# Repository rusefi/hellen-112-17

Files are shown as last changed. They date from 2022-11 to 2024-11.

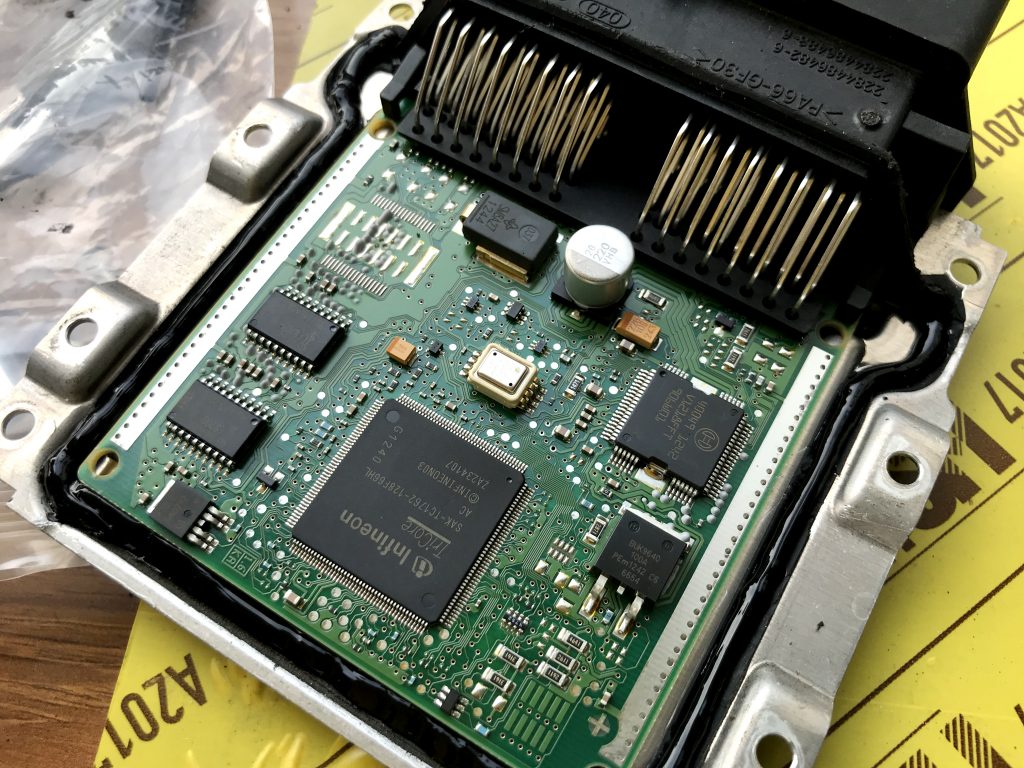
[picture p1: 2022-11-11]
docs/oem.jpg

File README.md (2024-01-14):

# hellen-112-17

[User Documentation](https://github.com/rusefi/rusefi/wiki/Hellen112-17)

[Interactive Pinout](https://rusefi.com/docs/pinouts/hellen/hellen-112-17/)

[Firmware Source Code](https://github.com/rusefi/rusefi/tree/master/firmware/config/boards/hellen/hellen-112-17)

# Compatibility

Bosch 21126-1411020-45

Bosch 21126-1411020-49

Bosch 21126-1411020-70

Suzuki 33910-69L01

Polaris Slingshot 4015316

Maybe 391F2-03FA0 HYUNDAI I20 1.2 16V?

Maybe 39124-2B500 KIA FORTE 1.6?

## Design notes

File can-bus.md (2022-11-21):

https://trekberry.ru/stat/rabota_s_can_shinoi_na_avtomobilie_lada_granta

ID 481 1 байт Двери 0 Закрыта, 128 Дверь водителя, 32 пасажира,160 передние двери открыты

ID 481 3 байтаварийка открытие багажника 31 поворотник на право2 поворотник на лево

ID 421 1 байт8 паркинг16 задняя24 нейтралка32 драйв72 2 скорость64 1 скорость

ID 498 1 байт ремень волителя65 пристегнут64 нет

ID 2DE 3 байт ручник0 опущен1 поднят5 или 4 включен ближний свет

ID 481 4 байт 1 моргнуть дальним

ID 160 6 байт педаль газа

ID 255 отпущена56 нажна в пол

==================
https://habr.com/ru/post/653615/

BU_: ECM ABS SRS 
BO_ 384 ECM_180: 8 ECM
   SG_ rpm : 7|16@0+ (0.125,0) [0|0] "rpm" Vector__XXX

BO_ 505 ECM_1F9: 8 ECM
   SG_ speed_km_h : 23|16@0+ (0.01,0) [0|0] "" Vector__XXX

BO_ 852 ABS_354: 8 ABS
   SG_ abs_lamp_on : 55|1@0+ (1,0) [0|1] "" Vector__XXX

BO_ 1176 SRS_498: 1 SRS
   SG_ airbag_lamp : 4|1@1+ (1,0) [0|0] "" Vector__XXX
   SG_ seatbelt_fastened : 0|1@1+ (1,0) [0|0] "" Vector__XXX

BO_ 1361 ECM_551: 8 ECM
   SG_ coolant_temperature : 15|8@0+ (1,-40) [0|0] "" Vector__XXX
   SG_ check_engine_lamp_on : 32|1@1+ (1,0) [0|0] "" Vector__XXX
   SG_ check_engine_lamp_blinking : 33|1@1+ (1,0) [0|0] "" Vector__XXX
   SG_ oil_lamp_on : 34|1@1+ (1,0) [0|0] "" Vector__XXX
   SG_ overheat_lamp_with_sound : 35|1@1+ (1,0) [0|0] "" Vector__XXX
   SG_ battery_lamp_off : 24|1@1+ (1,0) [0|0] "" Vector__XXX

   ==============================

   0x160 — педаль газа, дроссель
0x180 — обороты мотора, некоторые параметры по мотору
0x280 — приборы, скорость
0x481 — двери, световые приборы, подогревы
0x551 — приборы
0x555 — климат-контроль
0x560 — АКП

=======================

https://habr.com/ru/post/479672/comments/#comment_24929006



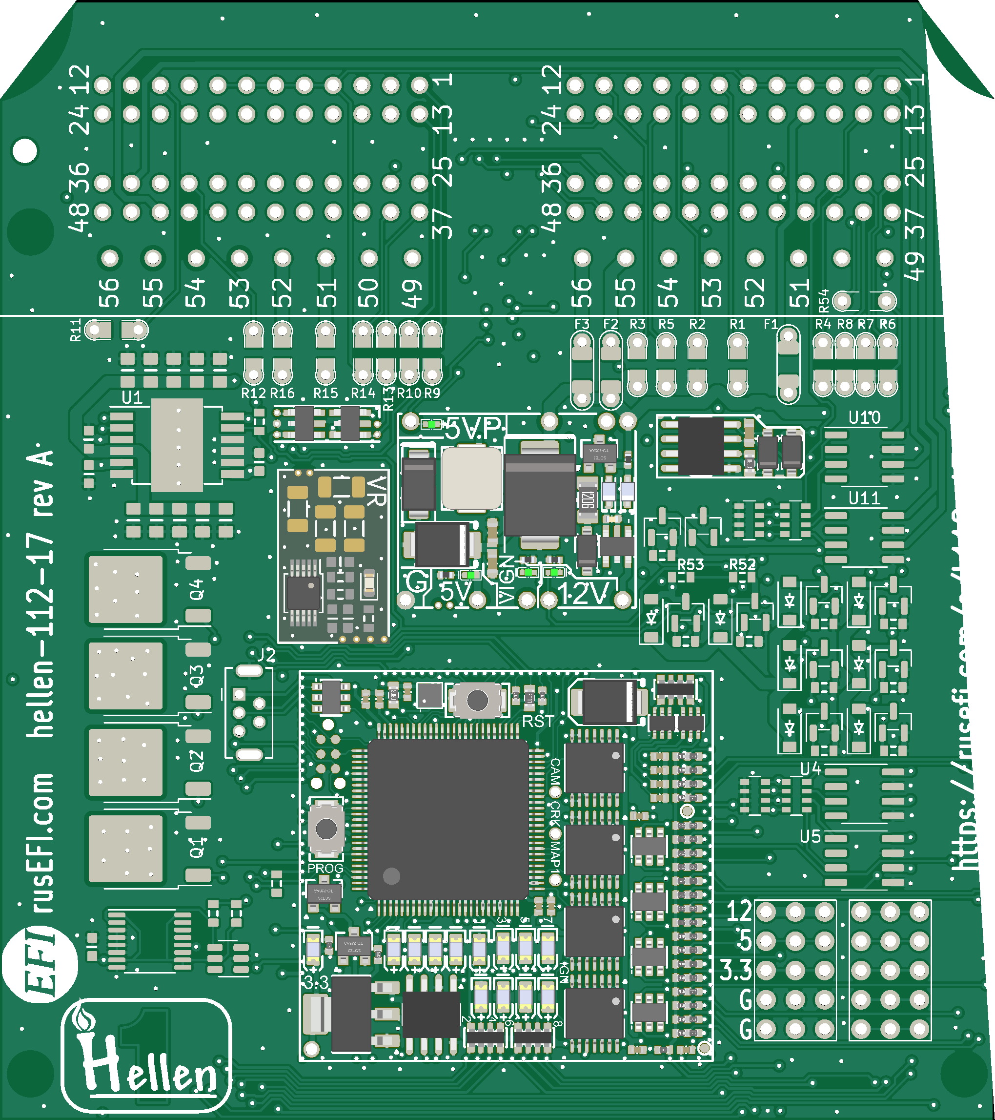
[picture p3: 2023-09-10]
boards/hellen-112-17-a/board/hellen-112-17-a.png

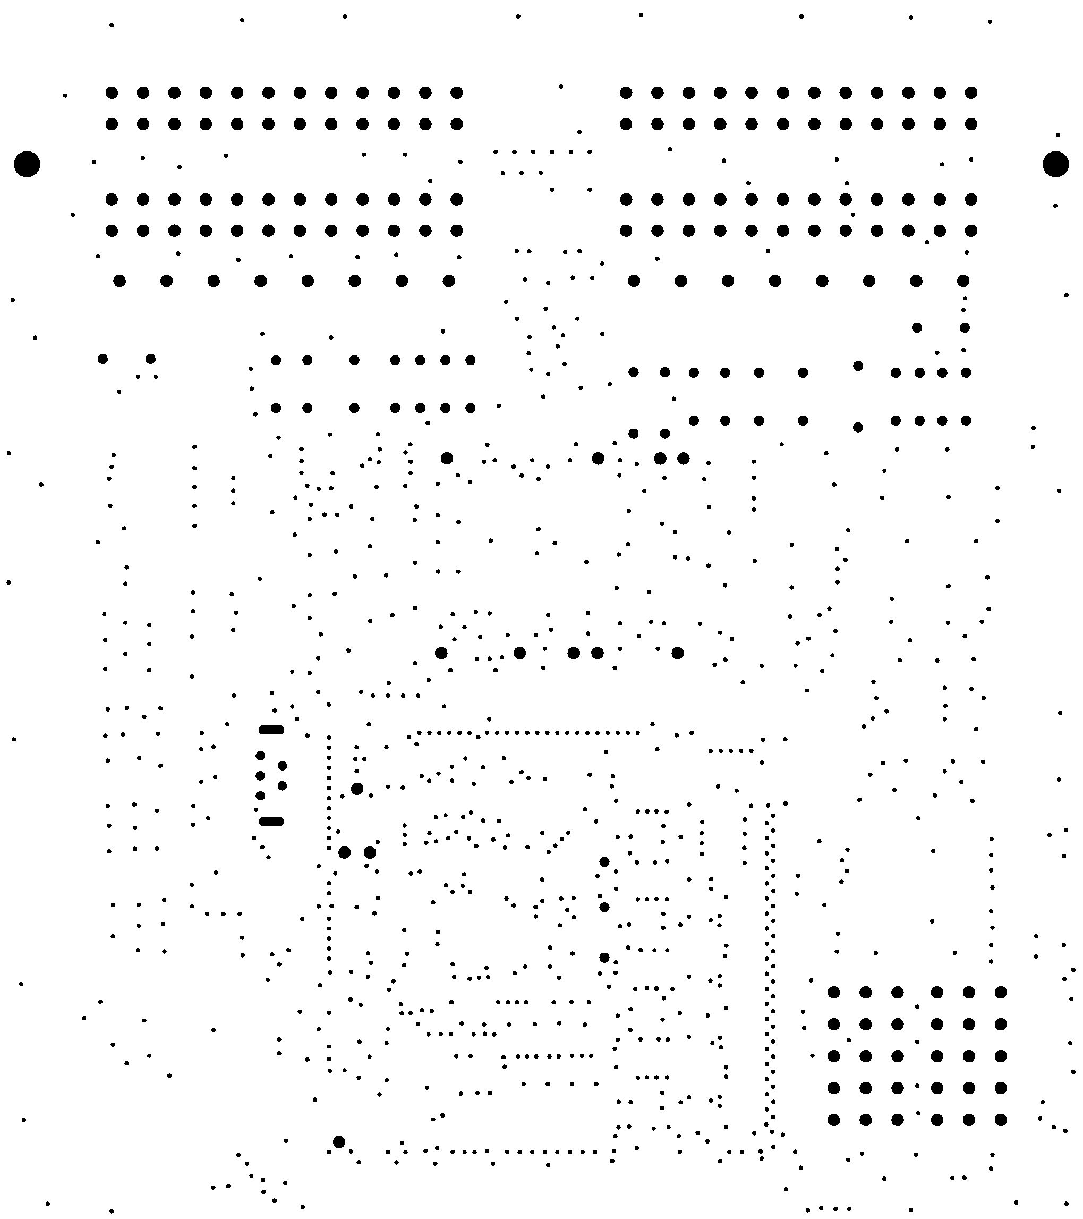
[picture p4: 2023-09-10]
boards/hellen-112-17-a/board/misc/hellen-112-17-a-outline.png

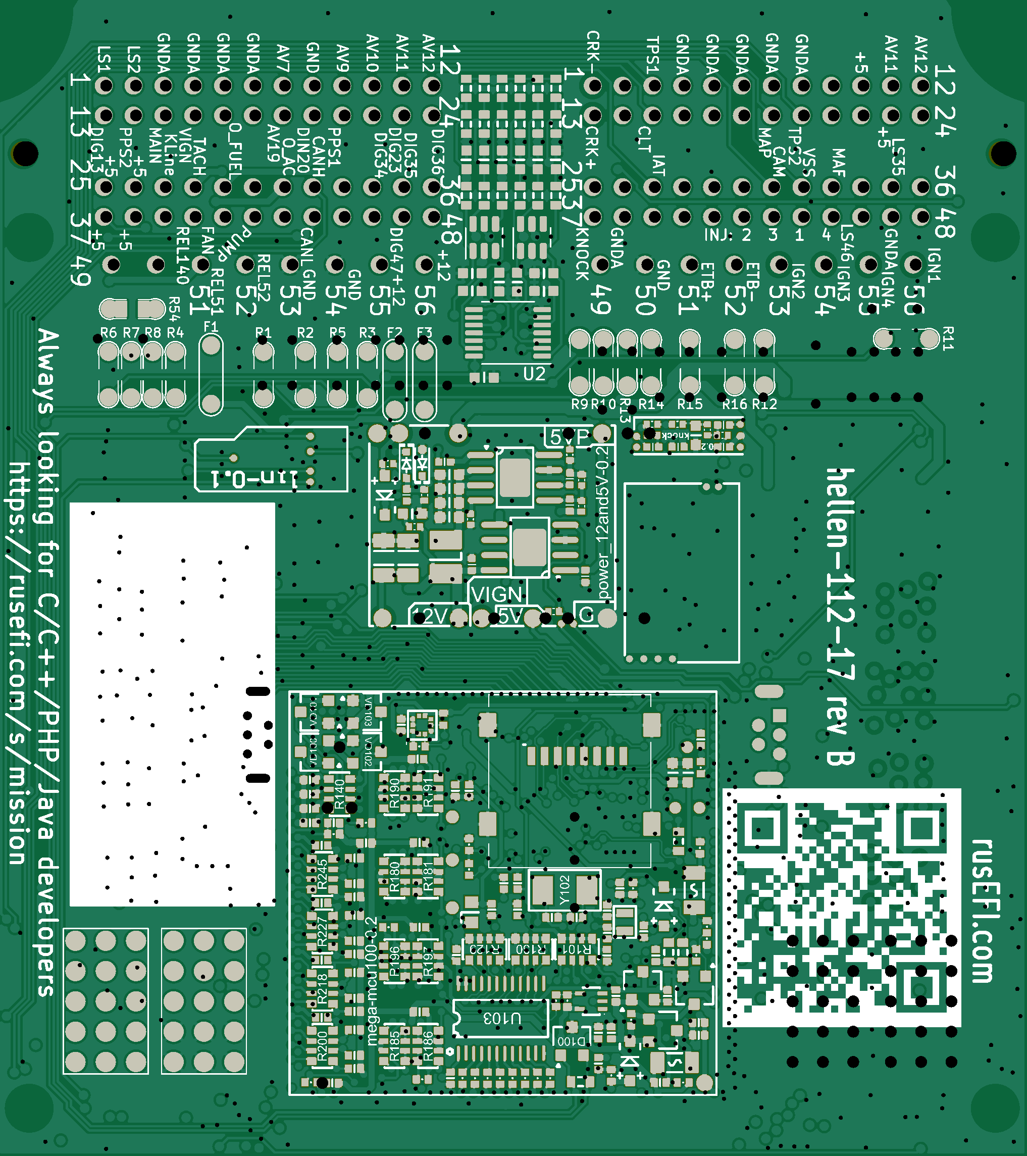
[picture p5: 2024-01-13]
boards/hellen-112-17-b/board/misc/hellen-112-17-b-bottom.png

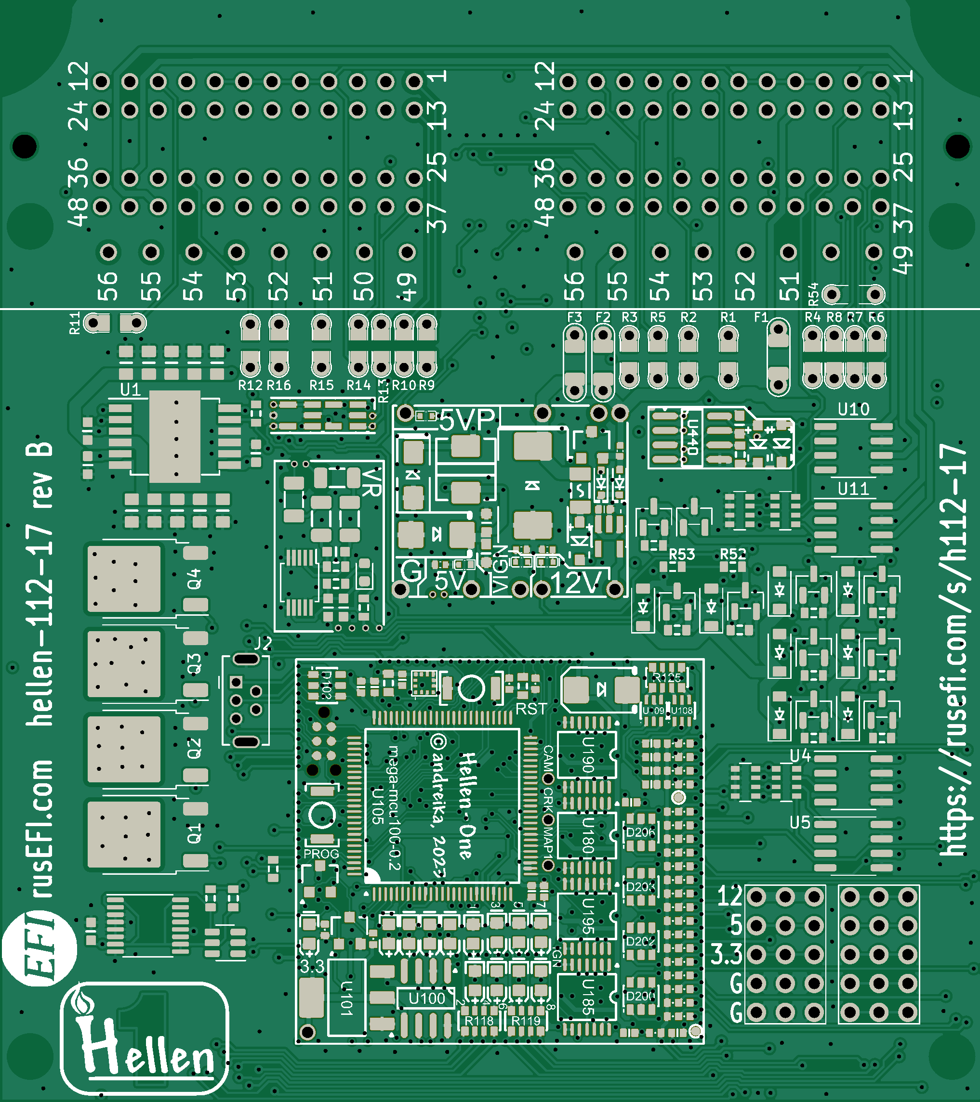
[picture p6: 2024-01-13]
boards/hellen-112-17-b/board/misc/hellen-112-17-b-top.png

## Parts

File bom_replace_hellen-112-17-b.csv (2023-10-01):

# remove +5V pull-ups from SPI1, because we use it with +3.3v accelerometer
R103,
R105,
# remove jumper resistor connecting BOOT1 with A22 input line, because we use STM32F4
R131,
#CAN wakeup disabled, O2S input enabled
R145,
#PWR_EN not used as GPIO
R142,
#IGBT series resistor
"R114, R115, R116, R117","33","R0402","C25105"
# DC-DC Inductor
L421,"MWSA0503S-100MT","MWSA0503","C408412"
# fuses
F410,"nSMD050-24V","SMD1206","C70076"
# TLS115
U411,"TLS115B0EJXUMA1","PG-DSO-8","C3743696"
# no software for accelerometer
U106,
# STM32F407VGT6 is very cheap
U105,"STM32F429VGT6","LQFP100","C12345"
#include hellen-one/board_id/generated/board_id_h112-17-b.csv
#include bom_pullups_hellen-112-17-b.csv

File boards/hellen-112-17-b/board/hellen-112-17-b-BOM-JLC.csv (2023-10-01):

Comment | Designator | Footprint | LCSC Part #
10u | C1, C2, C3, C4, C5, C6, C7, C8, C9, C10 | C0805 | C15850
100n | C11, C14, C21, C772, C440 | C0603 | C14663
10n | C12, C13 | C0603 | C57112
1n | C15, C16, C17, C18, C19, C20, C22, C23, C24, C25, C26, C28, C771 | C0603 | C1588
PSM712-LF | D1, D411 | SOT-23 | C32677
B5819W | D2, D3, D4, D5, D6, D7, D8, D9, D416, D417, D101, D107, D440, D441 | SOD-123 | C8598
SRV05-4-P-T7 | D10, D11, D12, D102, D200, D202, D203, D206 | SOT23-6 | C85364
12H1500D | F1, F2, F3 | PAD-1206-PAD | C182446
USB_B_Mini | J2 | USB-MINI-B-VERTICAL | C13453
ISL9V3040D3S | Q1, Q2, Q3, Q4 | DPAK | C462128
AO3400A | Q5, Q6, Q7, Q8, Q9, Q10, Q11, Q12, Q13, Q101, Q103 | SOT-23 | C20917
Jumper-Pad-Pad | R1, R2, R3, R4, R5, R6, R7, R8, R9, R10, R11, R12, R13, R14, R15, R16, R54 | PAD-0805-PAD | C17477
4.7k | R17, R18, R19, R20, R25, R26, R27, R28, R33, R34, R35, R36, R37, R38, R39, R40, R41, R50, R51, R52, R53 | R0603 | C23162
10k | R30, R31, R32, R42, R43, R48, R776, R777 | R0603 | C25804
1k | R44, R45, R46, R47 | R_Array_Convex_4x0603 | C20197
TLE9201SG | U1 | Infineon_PG-DSO-12-11 | C112633
74HC14PW,118 | U2 | TSSOP14 | C5606
VNLD5160 | U4, U5, U10, U11 | SO8 | C377942
74VHC163FT | U7 | TSSOP-16_4.4x5mm_P0.65mm | C150161
47u | C410, C412 | C1206 | C96123
100n | C411, C413, C420, C470 | C0402 | C307331
1u | C414, C415, C133 | C0402 | C52923
10u | C421, C422, C423, C424, C425, C426 | C0603 | C96446
4.7u | C427 | C0603 | C19666
10n | C428, C209, C203, C202, C201, C200, C214, C215, C212, C213, C225, C226, C227, C228, C145, C146 | C0402 | C15195
220p | C429 | C0402 | C1530
1N4148WS | D410, D412, D413, D414 | SOD-323 | C2128
SMCJ30A | D418 | SMC | C310046
SS34 | D420 | SMA | C8678
P6SMB6.8CA | D421, D205 | SMB | C78395
2.2uH | L420 | L1210 | C36828
MHT136UGCT | LED1, LED2, LED3, LED4 | LED0402 | C434447
6.8k | R410, R413 | R0402 | C25917
33k | R411, R424, R425, R474 | R0402 | C25779
1 | R420 | R0402 | C25086
10k | R421, R426, R427, R102, R107, R108, R109, R121, R127, R128, R141 | R0402 | C25744
68k | R422 | R0402 | C36871
12k | R423, R472 | R0402 | C25752
4.7k | R428, R144, R202, R201, R124, R126, R132, R135 | R0402 | C25900
MIC5205-3.3YM5 | U410 | SOT23-5 | C37970
LMR14020 | U420 | SOP8 | C187824
22u | C773, C117, C123 | C0603 | C59461
LED-GREEN-0603 | D771, D104, D108 | LED-0603 | C72043
4.7k | R771, R772, R773, R774 | R1206 | C17936
MAX9924UAUB+ | U771 | MSOP-10_3x3mm_P0.5mm | C143633
3.3n | C471 | C0402 | C26404
330p | C472 | C0402 | C13533
47p | C473 | C0402 | C1567
680p | C474 | C0603 | C1630
470k | R470 | R0402 | C25790
100k | R471, R473 | R0402 | C25741
LMV321IDBVR | U470, U471 | SOT23-5 | C7972
TJA1051T/3/1J | U100 | SO8 | C38695
SN74LVC4245APWR | U103 | TSSOP24 | C7859
SN74LVC1G06DCKR | U110 | SOT-353 | C7828
SMD1206B035TF/16 | F100, F101 | R1206 | C269114
REF3033 | U102 | SOT-23 | C36658
PESD1CAN | D100 | SOT-23 | C343993
Molex MicroSD 47219-2001 | J100 | SDAMB-012 | C164170
MCP6004 | U180, U185, U190, U195 | TSSOP14 | C50282
LPS22HBTR | U107 | HLGA-10L | C94049
LED-YELLOW-0603 | D106 | LED-0603 | C72038
LED-RED-0603 | D103 | LED-0603 | C2286
LED-BLUE-0603 | D105, D109, D110, D111, D112, D113, D114, D115, D116 | LED-0603 | C72041
LDL1117S33R | U101 | SOT-223 | C435835
BTN | S100, S101 | SMD-2_2.9x3.9x1.7 | C115357
BLM18AG601SN1D | L100 | L0603 | C19330
BAT54S | VD100, VD101, VD102, VD103 | SOT-23 | C47546
AO3401A | Q100, Q102 | SOT-23 | C15127
680k | R224, R208, R207, R234, R235, R232, R233, R250, R251, R252, R253, R225 | R0402 | C163456
510 | R254, R255, R256, R258 | R0402 | C25123
470 | R101, R118, R119 | R0603-4 | C25510
120 | R100 | R0603 | C22787
100n | C100, C101, C105, C108, C111, C112, C113, C119, C120, C122, C124, C126, C127, C130, C134, C147, C180, C185, C190, C195, C220, C221, C222 | C0402 | C1525
100 | R104, R106 | R0603 | C22775
74LVC2G17GW,125 | U108, U109 | SOT-363 | C80500
33k | R120 | R0603 | C4216
32.768 kHz | Y101 | SMD2012 | C99009
20 MHz | Y102 | SMD5032 | C112566
18p | C132, C136 | C0402 | C1549
12p | C115, C116 | C0402 | C1547
10k | R129, R130, R140 | R0603-4 | C29718
10 | R110, R111, R112, R113 | R0402 | C25077
5.1k | R195 | R0402 | C25905
4.7u | C102, C103, C104, C106, C107, C137, C138, C140 | C0402 | C23733
4.7k | R125, R180, R181, R185, R186, R190, R191, R196, R197, R200, R218, R227, R245 | R0603-4 | C66697
2.2u | C114, C131, C223, C224, C229 | C0402 | C12530
2.2k | R122, R123, R146, R147 | R0402 | C25879
1n | C135, C139, C141, C142, C211, C208, C210, C143, C144 | C0402 | C1523
0 | R143, R148 | R0402 | C17168
1k | R440 | R0603 | C21190
TJA1021T/20/CM | U440 | SO8 | C128810
33 | R114, R115, R116, R117 | R0402 | C25105
MWSA0503S-100MT | L421 | MWSA0503 | C408412
nSMD050-24V | F410 | SMD1206 | C70076
TLS115B0EJXUMA1 | U411 | PG-DSO-8 | C3743696
STM32F429VGT6 | U105 | LQFP100 | C12345
750 | R133 | R0603 | C23241
6800 | R134 | R0603 | C23212

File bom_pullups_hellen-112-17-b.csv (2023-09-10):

#CRANK CRANK_VR: UP DNP 1n
R222,
R226,
C211,"1n","C0402","C1523"
#CAM AV_107: DOWN 680k 10n
R220,
R224,"680k","R0402","C163456"
C209,"10n","C0402","C15195"
#VSS MAF: UP DNP 1n
R219,
R223,
C208,"1n","C0402","C1523"
#TPS TPS1: DOWN 680k 10n
R204,
R208,"680k","R0402","C163456"
C203,"10n","C0402","C15195"
#PPS PPS1: DOWN 680k 10n
R203,
R207,"680k","R0402","C163456"
C202,"10n","C0402","C15195"
#IAT IAT: UP 4.7k 10n
R202,"4.7k","R0402","C25900"
R206,
C201,"10n","C0402","C15195"
#CLT CLT: UP 4.7k 10n
R201,"4.7k","R0402","C25900"
R205,
C200,"10n","C0402","C15195"
#O2S TPS2: DOWN 680k 10n
R230,
R234,"680k","R0402","C163456"
C214,"10n","C0402","C15195"
#O2S2 PPS2: DOWN 680k 10n
R231,
R235,"680k","R0402","C163456"
C215,"10n","C0402","C15195"
#MAP1 MAP: DOWN 680k 10n
R228,
R232,"680k","R0402","C163456"
C212,"10n","C0402","C15195"
#MAP2 AV_109: DOWN 680k 10n
R229,
R233,"680k","R0402","C163456"
C213,"10n","C0402","C15195"
#AUX1 AV_110: DOWN 680k 10n
R246,
R250,"680k","R0402","C163456"
C225,"10n","C0402","C15195"
#AUX2 AV_111: DOWN 680k 10n
R247,
R251,"680k","R0402","C163456"
C226,"10n","C0402","C15195"
#AUX3 AV_112: DOWN 680k 10n
R248,
R252,"680k","R0402","C163456"
C227,"10n","C0402","C15195"
#AUX4 AV_119: DOWN 680k 10n
R249,
R253,"680k","R0402","C163456"
C228,"10n","C0402","C15195"
#KNOCK KNOCK: DOWN 680k 1n
R221,
R225,"680k","R0402","C163456"
C210,"1n","C0402","C1523"
#D1 CAM: UP 4.7k 1n
R124,"4.7k","R0402","C25900"
R136,
C143,"1n","C0402","C1523"
#D2 VSS: UP 4.7k 1n
R126,"4.7k","R0402","C25900"
R137,
C144,"1n","C0402","C1523"
#D3 DIGITAL_113: UP 4.7k 10n
R132,"4.7k","R0402","C25900"
R138,
C145,"10n","C0402","C15195"
#D4 DIGITAL_120: UP 4.7k 10n
R135,"4.7k","R0402","C25900"
R139,
C146,"10n","C0402","C15195"

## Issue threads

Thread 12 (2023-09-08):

изменения в распиновке

rusefillc, 2023-09-08:
https://github.com/rusefi/rusefi/commit/9bc75bf3ef2a4f8ac3f90c525db7b07e5ac62391 - там же пометки пинов, где точно нужны джамперы

Qwerty-OFF, 2023-09-08:
Все джамперы по умолчанию установлены?

rusefillc, 2023-09-08:
> Все джамперы по умолчанию установлены?

да

Closed 2023-09-10.

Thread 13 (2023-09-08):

digital inputs note

rusefillc, 2023-09-08:
мы сейчас такие поддерживаем? или у нас обычно подтяжки?

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

Qwerty-OFF, 2023-09-08:
Подтяжки к земле поддерживаем

Qwerty-OFF, 2023-09-10:
Подтяжки к земле по умолчанию. Если что, можно переставить резистор для подтяжки вверх.
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

Closed 2023-09-10.

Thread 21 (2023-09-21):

rev A test log was обжёгся в районе кнопки PROG

rusefillc, 2023-09-21:
получил две собранные платы
нажал PROG
подключил mini-UBS
обжёгся где-то в районе нажал PROG

один синий светодиод на блоке питания горит постоянно, второй медленно мигает
DFU устройство в Windows не появилось

rusefillc, 2023-09-21:
with pin lifted I was able to DFU program

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

Qwerty-OFF, 2023-10-01:
Починено в ММ100_0.2

Closed 2023-10-01.

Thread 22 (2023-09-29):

мигает не то

rusefillc, 2023-09-29:
ожидаемое поведение: мигает синий, остальные выключены

реальность: мигает красных, остальные тускло горят. инвертированны?

rusefillc, 2023-09-29:
```
#define MM100_LED1_RED D4
#define MM100_LED2_GREEN D7
#define MM100_LED3_BLUE E7
#define MM100_LED4_YELLOW E8
```

rusefillc, 2023-09-29:
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

rusefillc, 2023-09-29:
на всех хеллен прошивках одинаково
```
DDEFS += -DLED_PIN_MODE=OM_INVERTED
```

rusefillc, 2023-09-29:
just noticed that green LED on MAX9924 VR is blinking, overall we clearly have a reboot cycle

things are proper with EN output disabled!

rusefillc, 2023-09-29:
worked better without EN

works better with EN without fuse

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

rusefillc, 2023-09-30:
returned the fuse

works without three passives

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

works once capacitors were removed

final conclusion: blame bad resistor or soldering at the resisitor?

Closed 2023-09-30.

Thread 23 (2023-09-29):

DFU USB works but no USB serial

rusefillc, 2023-09-29:
SW or HW issue?

rusefillc, 2023-09-29:
firmware has USB by default
```
#ifndef EFI_USB_SERIAL
#define EFI_USB_SERIAL TRUE
#endif
```

rusefillc, 2023-09-29:
using 112-17 firmware on f429-nucleo I get errors via USB
```
2023-09-29_15_04_45_970: EngineState: CRITICAL error: Pin "244 injector output 1" (PD7) required by "Injector 1" but is used by "led: running status" 20230929@hellen-112-17
```

meaning I suspect HW not SW

rusefillc, 2023-09-29:
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

rusefillc, 2023-09-29:
Duplicate of #22 - this is all just a reboot cycle

Closed 2023-09-29.

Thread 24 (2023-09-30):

rev A test log

rusefillc, 2023-09-30:
* with one stm32 pin removed USB works and blue LED blinkds
* powers from +12v
* SD card works

rusefillc, 2023-11-29:
```
15/28 Fuel Relay GOOD channel 16
               Setting ADDR 0
               sending line=17 value=1
                          Processing BENCH_TEST_IO_META_INFO ID=770005/l=8 66 0 13 13 1 0 0 0
       CAN ECU says: total=19 outputs of which low side=19 also 1 DC
                          Processing BENCH_TEST_BOARD_STATUS ID=770003/l=8 0 D3 0 1 EF 0 63 0
                          Processing BENCH_TEST_BUTTON_COUNTERS ID=770004/l=8 0 0 0 0 0 0 0 0
                          Processing BENCH_TEST_EVENT_COUNTERS ID=770000/l=8 0 0 0 0 0 0 0 0
                          Processing BENCH_TEST_RAW_ANALOG_1 ID=770001/l=8 1B 29 2C 32 20 50 2C 70
                          Processing BENCH_TEST_RAW_ANALOG_2 ID=770006/l=8 0 0 0 0 0 0 0 0
                      ADC says HIGH 17@0 3.057v
               sending line=17 value=0
                          Processing BENCH_TEST_EVENT_COUNTERS ID=770000/l=8 0 0 0 0 0 0 0 0
                          Processing BENCH_TEST_RAW_ANALOG_1 ID=770001/l=8 1B 29 2C 32 20 50 2C 70
                          Processing BENCH_TEST_RAW_ANALOG_2 ID=770006/l=8 0 0 0 0 0 0 0 0
                      ADC says LOW 17@1 0.003v
               sending line=17 value=1
                          Processing BENCH_TEST_EVENT_COUNTERS ID=770000/l=8 0 0 0 0 0 0 0 0
                          Processing BENCH_TEST_RAW_ANALOG_1 ID=770001/l=8 1B 29 2C 32 20 50 2C 70
                          Processing BENCH_TEST_RAW_ANALOG_2 ID=770006/l=8 0 0 0 0 0 0 0 0
                          Processing BENCH_TEST_IO_META_INFO ID=770005/l=8 66 0 13 13 1 0 0 0
       CAN ECU says: total=19 outputs of which low side=19 also 1 DC
                          Processing BENCH_TEST_BOARD_STATUS ID=770003/l=8 0 D3 0 1 EF 0 63 0
                          Processing BENCH_TEST_BUTTON_COUNTERS ID=770004/l=8 0 0 0 0 0 0 0 0
               sending line=17 value=0
                          Processing BENCH_TEST_EVENT_COUNTERS ID=770000/l=8 0 0 0 0 0 0 0 0
                          Processing BENCH_TEST_RAW_ANALOG_1 ID=770001/l=8 1B 29 2C 32 20 50 2C 70
                          Processing BENCH_TEST_RAW_ANALOG_2 ID=770006/l=8 0 0 0 0 0 0 0 0
16/28 pin 151 GOOD channel 17
               Setting ADDR 1
               sending line=18 value=1
                          Processing BENCH_TEST_EVENT_COUNTERS ID=770000/l=8 0 0 0 0 0 0 0 0
                          Processing BENCH_TEST_RAW_ANALOG_1 ID=770001/l=8 1B 29 2C 32 20 4F 2C 70
                          Processing BENCH_TEST_RAW_ANALOG_2 ID=770006/l=8 0 0 0 0 0 0 0 0
                      ADC says HIGH 18@0 3.056v
               sending line=18 value=0
                          Processing BENCH_TEST_IO_META_INFO ID=770005/l=8 66 0 13 13 1 0 0 0
       CAN ECU says: total=19 outputs of which low side=19 also 1 DC
                          Processing BENCH_TEST_BOARD_STATUS ID=770003/l=8 0 D3 0 1 EF 0 63 0
                          Processing BENCH_TEST_BUTTON_COUNTERS ID=770004/l=8 0 0 0 0 0 0 0 0
                          Processing BENCH_TEST_EVENT_COUNTERS ID=770000/l=8 0 0 0 0 0 0 0 0
                          Processing BENCH_TEST_RAW_ANALOG_1 ID=770001/l=8 1B 29 2C 32 20 4F 2C 70
                          Processing BENCH_TEST_RAW_ANALOG_2 ID=770006/l=8 0 0 0 0 0 0 0 0
                      ADC says LOW 18@1 0.002v
               sending line=18 value=1
                          Processing BENCH_TEST_EVENT_COUNTERS ID=770000/l=8 0 0 0 0 0 0 0 0
                          Processing BENCH_TEST_RAW_ANALOG_1 ID=770001/l=8 1B 29 2C 32 20 4F 2C 70
                          Processing BENCH_TEST_RAW_ANALOG_2 ID=770006/l=8 0 0 0 0 0 0 0 0
               sending line=18 value=0
                          Processing BENCH_TEST_EVENT_COUNTERS ID=770000/l=8 0 0 0 0 0 0 0 0
                          Processing BENCH_TEST_RAW_ANALOG_1 ID=770001/l=8 1B 29 2C 32 20 4F 2C 70
                          Processing BENCH_TEST_RAW_ANALOG_2 ID=770006/l=8 0 0 0 0 0 0 0 0
                          Processing BENCH_TEST_IO_META_INFO ID=770005/l=8 66 0 13 13 1 0 0 0
       CAN ECU says: total=19 outputs of which low side=19 also 1 DC
                          Processing BENCH_TEST_BOARD_STATUS ID=770003/l=8 0 D3 0 1 EF 0 63 0
                          Processing BENCH_TEST_BUTTON_COUNTERS ID=770004/l=8 0 0 0 0 0 0 0 0
17/28 pin 152 GOOD channel 18
               Setting ADDR 2
               sending line=19 value=1
                          Processing BENCH_TEST_EVENT_COUNTERS ID=770000/l=8 0 0 0 0 0 0 0 0
                          Processing BENCH_TEST_RAW_ANALOG_1 ID=770001/l=8 1B 29 2C 32 20 4F 2C 70
                          Processing BENCH_TEST_RAW_ANALOG_2 ID=770006/l=8 0 0 0 0 0 0 0 0
                      ADC says HIGH 19@0 3.054v
               sending line=19 value=0
                          Processing BENCH_TEST_EVENT_COUNTERS ID=770000/l=8 0 0 0 0 0 0 0 0
                          Processing BENCH_TEST_RAW_ANALOG_1 ID=770001/l=8 1B 29 2C 32 20 4F 2C 70
                          Processing BENCH_TEST_RAW_ANALOG_2 ID=770006/l=8 0 0 0 0 0 0 0 0
                      ADC says LOW 19@1 0.004v
               sending line=19 value=1
                          Processing BENCH_TEST_IO_META_INFO ID=770005/l=8 66 0 13 13 1 0 0 0
       CAN ECU says: total=19 outputs of which low side=19 also 1 DC
                          Processing BENCH_TEST_BOARD_STATUS ID=770003/l=8 0 D3 0 1 F0 0 63 0
                          Processing BENCH_TEST_BUTTON_COUNTERS ID=770004/l=8 0 0 0 0 0 0 0 0
                          Processing BENCH_TEST_EVENT_COUNTERS ID=770000/l=8 0 0 0 0 0 0 0 0
                          Processing BENCH_TEST_RAW_ANALOG_1 ID=770001/l=8 1B 29 2C 32 20 4F 2C 70
                          Processing BENCH_TEST_RAW_ANALOG_2 ID=770006/l=8 0 0 0 0 0 0 0 0
               sending line=19 value=0
                          Processing BENCH_TEST_EVENT_COUNTERS ID=770000/l=8 0 0 0 0 0 0 0 0
                          Processing BENCH_TEST_RAW_ANALOG_1 ID=770001/l=8 1B 29 2C 32 20 4F 2C 70
                          Processing BENCH_TEST_RAW_ANALOG_2 ID=770006/l=8 0 0 0 0 0 0 0 0
18/28 pin 246 GOOD channel 19
19/28      Toggling port 0
                          Processing BENCH_TEST_EVENT_COUNTERS ID=770000/l=8 0 0 1 0 0 0 0 0
                          Processing BENCH_TEST_RAW_ANALOG_1 ID=770001/l=8 1B 29 2C 32 20 4F 2C 70
                          Processing BENCH_TEST_RAW_ANALOG_2 ID=770006/l=8 0 0 0 0 0 0 0 0
                          Processing BENCH_TEST_IO_META_INFO ID=770005/l=8 66 0 13 13 1 0 0 0
       CAN ECU says: total=19 outputs of which low side=19 also 1 DC
                          Processing BENCH_TEST_BOARD_STATUS ID=770003/l=8 0 D3 0 1 F0 0 63 0
                          Processing BENCH_TEST_BUTTON_COUNTERS ID=770004/l=8 0 0 0 0 0 0 0 0
                          Processing BENCH_TEST_EVENT_COUNTERS ID=770000/l=8 0 0 2 0 0 0 0 0
                          Processing BENCH_TEST_RAW_ANALOG_1 ID=770001/l=8 1B 29 2C 32 20 4F 2C 70
                          Processing BENCH_TEST_RAW_ANALOG_2 ID=770006/l=8 0 0 0 0 0 0 0 0
                          Processing BENCH_TEST_EVENT_COUNTERS ID=770000/l=8 0 0 3 0 0 0 0 0
                          Processing BENCH_TEST_RAW_ANALOG_1 ID=770001/l=8 1B 29 2C 32 20 4F 2C 70
                          Processing BENCH_TEST_RAW_ANALOG_2 ID=770006/l=8 0 0 0 0 0 0 0 0
                          Processing BENCH_TEST_IO_META_INFO ID=770005/l=8 66 0 13 13 1 0 0 0
       CAN ECU says: total=19 outputs of which low side=19 also 1 DC
                          Processing BENCH_TEST_BOARD_STATUS ID=770003/l=8 0 D3 0 1 F0 0 63 0
                          Processing BENCH_TEST_BUTTON_COUNTERS ID=770004/l=8 0 0 0 0 0 0 0 0
                          Processing BENCH_TEST_EVENT_COUNTERS ID=770000/l=8 0 0 4 0 0 0 0 0
                          Processing BENCH_TEST_RAW_ANALOG_1 ID=770001/l=8 1B 29 2C 32 20 4F 2C 70
                          Processing BENCH_TEST_RAW_ANALOG_2 ID=770006/l=8 0 0 0 0 0 0 0 0
                          Processing BENCH_TEST_EVENT_COUNTERS ID=770000/l=8 0 0 5 0 0 0 0 0
                          Processing BENCH_TEST_RAW_ANALOG_1 ID=770001/l=8 1B 29 2C 32 20 4F 2C 70
                          Processing BENCH_TEST_RAW_ANALOG_2 ID=770006/l=8 0 0 0 0 0 0 0 0
                          Processing BENCH_TEST_EVENT_COUNTERS ID=770000/l=8 0 0 6 0 0 0 0 0
                          Processing BENCH_TEST_RAW_ANALOG_1 ID=770001/l=8 1B 29 2C 32 20 4F 2C 70
                          Processing BENCH_TEST_RAW_ANALOG_2 ID=770006/l=8 0 0 0 0 0 0 0 0
                          Processing BENCH_TEST_IO_META_INFO ID=770005/l=8 66 0 13 13 1 0 0 0
       CAN ECU says: total=19 outputs of which low side=19 also 1 DC
                          Processing BENCH_TEST_BOARD_STATUS ID=770003/l=8 0 D3 0 1 F0 0 63 0
                          Processing BENCH_TEST_BUTTON_COUNTERS ID=770004/l=8 0 0 0 0 0 0 0 0
                          Processing BENCH_TEST_EVENT_COUNTERS ID=770000/l=8 0 0 7 0 0 0 0 0
                          Processing BENCH_TEST_RAW_ANALOG_1 ID=770001/l=8 1B 29 2C 32 20 4F 2C 70
                          Processing BENCH_TEST_RAW_ANALOG_2 ID=770006/l=8 0 0 0 0 0 0 0 0
                          Processing BENCH_TEST_EVENT_COUNTERS ID=770000/l=8 0 0 8 0 0 0 0 0
                          Processing BENCH_TEST_RAW_ANALOG_1 ID=770001/l=8 1B 29 2C 32 20 4F 2C 70
                          Processing BENCH_TEST_RAW_ANALOG_2 ID=770006/l=8 0 0 0 0 0 0 0 0
                          Processing BENCH_TEST_IO_META_INFO ID=770005/l=8 66 0 13 13 1 0 0 0
       CAN ECU says: total=19 outputs of which low side=19 also 1 DC
                          Processing BENCH_TEST_BOARD_STATUS ID=770003/l=8 0 D3 0 1 F1 0 63 0
                          Processing BENCH_TEST_BUTTON_COUNTERS ID=770004/l=8 0 0 0 0 0 0 0 0
                          Processing BENCH_TEST_EVENT_COUNTERS ID=770000/l=8 0 0 9 0 0 0 0 0
                          Processing BENCH_TEST_RAW_ANALOG_1 ID=770001/l=8 1B 29 2C 32 20 4F 2C 70
                          Processing BENCH_TEST_RAW_ANALOG_2 ID=770006/l=8 0 0 0 0 0 0 0 0
                          Processing BENCH_TEST_EVENT_COUNTERS ID=770000/l=8 0 0 A 0 0 0 0 0
                          Processing BENCH_TEST_RAW_ANALOG_1 ID=770001/l=8 1B 29 2C 32 20 4F 2C 70
                          Processing BENCH_TEST_RAW_ANALOG_2 ID=770006/l=8 0 0 0 0 0 0 0 0
20/28      Toggling port 7
                          Processing BENCH_TEST_EVENT_COUNTERS ID=770000/l=8 0 0 A 0 0 0 1 0
                          Processing BENCH_TEST_RAW_ANALOG_1 ID=770001/l=8 1B 29 2C 32 20 4F 2C 70
                          Processing BENCH_TEST_RAW_ANALOG_2 ID=770006/l=8 0 0 0 0 0 0 0 0
                          Processing BENCH_TEST_IO_META_INFO ID=770005/l=8 66 0 13 13 1 0 0 0
       CAN ECU says: total=19 outputs of which low side=19 also 1 DC
                          Processing BENCH_TEST_BOARD_STATUS ID=770003/l=8 0 D3 0 1 F1 0 63 0
                          Processing BENCH_TEST_BUTTON_COUNTERS ID=770004/l=8 0 0 0 0 0 0 0 0
                          Processing BENCH_TEST_EVENT_COUNTERS ID=770000/l=8 0 0 A 0 0 0 1 0
                          Processing BENCH_TEST_RAW_ANALOG_1 ID=770001/l=8 1B 29 2C 32 20 4F 2C 70
                          Processing BENCH_TEST_RAW_ANALOG_2 ID=770006/l=8 0 0 0 0 0 0 0 0
                          Processing BENCH_TEST_EVENT_COUNTERS ID=770000/l=8 0 0 A 0 0 0 2 0
                          Processing BENCH_TEST_RAW_ANALOG_1 ID=770001/l=8 1B 29 2C 32 20 4F 2C 70
                          Processing BENCH_TEST_RAW_ANALOG_2 ID=770006/l=8 0 0 0 0 0 0 0 0
                          Processing BENCH_TEST_IO_META_INFO ID=770005/l=8 66 0 13 13 1 0 0 0
       CAN ECU says: total=19 outputs of which low side=19 also 1 DC
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

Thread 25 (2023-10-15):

board id 110 is not right

rusefillc, 2023-10-15:
I have 112-17 board
```
2023-10-15_13_28_31_534: EngineState: * RESULT: BoardId = 110, R1 = 620.000000000, R2 = 3900.000000000 (Elapsed time: 324 ms)
```

while
```
"211","750","4700","h112-17-a"
```

rusefillc, 2023-10-15:
```
2023-10-15_13_28_31_525: EngineState: Hellen board pin states = 0 0
2023-10-15_13_28_31_526: EngineState: * Cannot detect Hellen mcu module!
2023-10-15_13_28_31_526: EngineState: Starting Hellen Board ID detection...
2023-10-15_13_28_31_527: EngineState: pin_markUsed: boardId on PD8
2023-10-15_13_28_31_527: EngineState: pin_markUnused: PD8
2023-10-15_13_28_31_528: EngineState: pin_markUsed: boardId on PD8
2023-10-15_13_28_31_528: EngineState: pin_markUnused: PD8
2023-10-15_13_28_31_529: EngineState: pin_markUsed: boardId on PD8
2023-10-15_13_28_31_529: EngineState: pin_markUnused: PD8
2023-10-15_13_28_31_529: EngineState: pin_markUsed: boardId on PD9
2023-10-15_13_28_31_530: EngineState: pin_markUnused: PD9
2023-10-15_13_28_31_530: EngineState: pin_markUsed: boardId on PD9
2023-10-15_13_28_31_531: EngineState: pin_markUnused: PD9
2023-10-15_13_28_31_533: EngineState: pin_markUsed: boardId on PD9
2023-10-15_13_28_31_533: EngineState: pin_markUnused: PD9
2023-10-15_13_28_31_533: EngineState: pin_markUnused: PD9
2023-10-15_13_28_31_534: EngineState: pin_markUnused: PD8
```

rusefillc, 2023-10-15:
https://github.com/rusefi/rusefi/issues/5615

rusefillc, 2023-10-15:
```
2023-10-15_14_13_11_768: EngineState: * Cannot figure if legacy 144 or 176 Hellen mcu module!
2023-10-15_14_13_11_770: EngineState: Starting Hellen Board ID detection...
2023-10-15_14_13_11_770: EngineState: *** Resistor R1...
2023-10-15_14_13_11_771: EngineState: pin_markUsed: boardId on PD9
2023-10-15_14_13_11_772: EngineState: * dTime2-1 = 11193
2023-10-15_14_13_11_773: EngineState: * dTime3-2 = 11193
2023-10-15_14_13_11_774: EngineState: * dTime4-3 = 6434
2023-10-15_14_13_11_774: EngineState: * Tc1 = 2798.250000000, Tc2 = 1608.500000000, Td = 2798.250000000
2023-10-15_14_13_11_775: EngineState: pin_markUnused: PD9
2023-10-15_14_13_11_776: EngineState: pin_markUsed: boardId on PD9
2023-10-15_14_13_11_776: EngineState: * dTime2-1 = 11181
2023-10-15_14_13_11_777: EngineState: * dTime3-2 = 11181
2023-10-15_14_13_11_777: EngineState: * dTime4-3 = 6435
2023-10-15_14_13_11_778: EngineState: * Tc1 = 2795.250000000, Tc2 = 1608.750000000, Td = 2795.250000000
2023-10-15_14_13_11_779: EngineState: pin_markUnused: PD9
2023-10-15_14_13_11_779: EngineState: pin_markUsed: boardId on PD9
2023-10-15_14_13_11_779: EngineState: * dTime2-1 = 11177
2023-10-15_14_13_11_780: EngineState: * dTime3-2 = 11177
2023-10-15_14_13_11_781: EngineState: * dTime4-3 = 6437
2023-10-15_14_13_11_781: EngineState: * Tc1 = 2794.250000000, Tc2 = 1609.250000000, Td = 2794.250000000
2023-10-15_14_13_11_782: EngineState: pin_markUnused: PD9
2023-10-15_14_13_11_782: EngineState: * [0] R = 510.000000000, delta = 7.050160408
2023-10-15_14_13_11_783: EngineState: * [1] R = 620.000000000, delta = 5.621906304
2023-10-15_14_13_11_783: EngineState: * [2] R = 750.000000000, delta = 4.474109184
2023-10-15_14_13_11_784: EngineState: * [3] R = 1000.000000000, delta = 3.105582240
2023-10-15_14_13_11_785: EngineState: * [4] R = 1200.000000000, delta = 2.421318304
2023-10-15_14_13_11_786: EngineState: * [5] R = 1500.000000000, delta = 1.737054592
2023-10-15_14_13_11_788: EngineState: * [6] R = 1800.000000000, delta = 1.280879008
2023-10-15_14_13_11_788: EngineState: * [7] R = 2200.000000000, delta = 0.866173632
2023-10-15_14_13_11_789: EngineState: * [8] R = 2700.000000000, delta = 0.520585888
2023-10-15_14_13_11_789: EngineState: * [9] R = 3300.000000000, delta = 0.244115712
2023-10-15_14_13_11_790: EngineState: * [10] R = 3900.000000000, delta = 0.052713396
2023-10-15_14_13_11_791: EngineState: * R = 3900.000000000, Rmeasured = 4127.582031232, Rest = 4033.655273408, Creal = 1.052415728
2023-10-15_14_13_11_792: EngineState: *** Resistor R2...
2023-10-15_14_13_11_792: EngineState: pin_markUsed: boardId on PD8
2023-10-15_14_13_11_793: EngineState: * dTime2-1 = 1830
2023-10-15_14_13_11_793: EngineState: * dTime3-2 = 1830
2023-10-15_14_13_11_794: EngineState: * dTime4-3 = 1058
2023-10-15_14_13_11_795: EngineState: * Tc1 = 457.500000000, Tc2 = 264.500000000, Td = 457.500000000
2023-10-15_14_13_11_795: EngineState: pin_markUnused: PD8
2023-10-15_14_13_11_796: EngineState: pin_markUsed: boardId on PD8
2023-10-15_14_13_11_796: EngineState: * dTime2-1 = 1830
2023-10-15_14_13_11_797: EngineState: * dTime3-2 = 1830
2023-10-15_14_13_11_798: EngineState: * dTime4-3 = 1059
2023-10-15_14_13_11_798: EngineState: * Tc1 = 457.500000000, Tc2 = 264.750000000, Td = 457.500000000
2023-10-15_14_13_11_799: EngineState: pin_markUnused: PD8
2023-10-15_14_13_11_799: EngineState: pin_markUsed: boardId on PD8
2023-10-15_14_13_11_800: EngineState: * dTime2-1 = 1829
2023-10-15_14_13_11_800: EngineState: * dTime3-2 = 1829
2023-10-15_14_13_11_801: EngineState: * dTime4-3 = 1058
2023-10-15_14_13_11_802: EngineState: * Tc1 = 457.250000000, Tc2 = 264.500000000, Td = 457.250000000
2023-10-15_14_13_11_803: EngineState: pin_markUnused: PD8
2023-10-15_14_13_11_803: EngineState: * [0] R = 510.000000000, delta = 0.205888512
2023-10-15_14_13_11_804: EngineState: * [1] R = 620.000000000, delta = 0.008059501
2023-10-15_14_13_11_805: EngineState: * R = 620.000000000, Rmeasured = 637.003112793, Rest = 627.045654296, Creal = 1.044223784
2023-10-15_14_13_11_805: EngineState: pin_markUnused: PD8
2023-10-15_14_13_11_806: EngineState: pin_markUnused: PD9
2023-10-15_14_13_11_807: EngineState: * RESULT: BoardId = 1001, R1 = 3900.000000000, R2 = 620.000000000 (Elapsed time: 325 ms)
```

rusefillc, 2023-10-20:
@Qwerty-OFF а можно картинку c помеченными board id резисторами? буду замерять

и для сравнения аналогичную картинку mm144

rusefillc, 2023-10-20:
hellen125honda rev A just for comparison
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
rusefillc, 2023-10-27:
without cap

```
2023-10-27_15_45_43_711: EngineState: Starting Hellen Board ID detection...
2023-10-27_15_45_43_711: EngineState: *** Resistor R1...
2023-10-27_15_45_43_712: EngineState: pin_markUsed: boardId on PD9
2023-10-27_15_45_43_713: EngineState: * Hellen Board ID circuitry wasn't detected! Aborting!
2023-10-27_15_45_43_713: EngineState: pin_markUnused: PD8
2023-10-27_15_45_43_713: EngineState: pin_markUnused: PD9
2023-10-27_15_45_43_714: EngineState: * RESULT: BoardId = -1, R1 = 0.000000000, R2 = 0.000000000 (Elapsed time: 50 ms)
```

rusefillc, 2023-10-27:
board1 with 5%

```
2023-10-27_15_52_50_137: EngineState: Starting Hellen Board ID detection...
2023-10-27_15_52_50_138: EngineState: *** Resistor R1...
2023-10-27_15_52_50_138: EngineState: pin_markUsed: boardId on PD9
2023-10-27_15_52_50_139: EngineState: * dTime2-1 = 15499
2023-10-27_15_52_50_139: EngineState: * dTime3-2 = 15499
2023-10-27_15_52_50_140: EngineState: * dTime4-3 = 9274
2023-10-27_15_52_50_140: EngineState: * Tc1 = 3874.750000000, Tc2 = 2318.500000000, Td = 3874.750000000
2023-10-27_15_52_50_141: EngineState: pin_markUnused: PD9
2023-10-27_15_52_50_141: EngineState: pin_markUsed: boardId on PD9
2023-10-27_15_52_50_142: EngineState: * dTime2-1 = 15108
2023-10-27_15_52_50_143: EngineState: * dTime3-2 = 15108
2023-10-27_15_52_50_143: EngineState: * dTime4-3 = 9126
2023-10-27_15_52_50_144: EngineState: * Tc1 = 3777.000000000, Tc2 = 2281.500000000, Td = 3777.000000000
2023-10-27_15_52_50_145: EngineState: pin_markUnused: PD9
2023-10-27_15_52_50_145: EngineState: pin_markUsed: boardId on PD9
2023-10-27_15_52_50_146: EngineState: * dTime2-1 = 15036
2023-10-27_15_52_50_146: EngineState: * dTime3-2 = 15036
2023-10-27_15_52_50_147: EngineState: * dTime4-3 = 9087
2023-10-27_15_52_50_147: EngineState: * Tc1 = 3759.000000000, Tc2 = 2271.750000000, Td = 3759.000000000
2023-10-27_15_52_50_148: EngineState: pin_markUnused: PD9
2023-10-27_15_52_50_149: EngineState: * [0] R = 510.000000000, delta = 9.279188160
2023-10-27_15_52_50_149: EngineState: * [1] R = 620.000000000, delta = 7.455460544
2023-10-27_15_52_50_150: EngineState: * [2] R = 750.000000000, delta = 5.989847680
2023-10-27_15_52_50_150: EngineState: * [3] R = 1000.000000000, delta = 4.242385872
2023-10-27_15_52_50_151: EngineState: * [4] R = 1200.000000000, delta = 3.368654720
2023-10-27_15_52_50_151: EngineState: * [5] R = 1500.000000000, delta = 2.494923840
2023-10-27_15_52_50_152: EngineState: * [6] R = 1800.000000000, delta = 1.912436480
2023-10-27_15_52_50_153: EngineState: * [7] R = 2200.000000000, delta = 1.382902624
2023-10-27_15_52_50_153: EngineState: * [8] R = 2700.000000000, delta = 0.941624384
2023-10-27_15_52_50_154: EngineState: * [9] R = 3300.000000000, delta = 0.588601728
2023-10-27_15_52_50_154: EngineState: * [10] R = 3900.000000000, delta = 0.344201440
2023-10-27_15_52_50_155: EngineState: * [11] R = 4700.000000000, delta = 0.115401272
2023-10-27_15_52_50_156: EngineState: * [12] R = 5600.000000000, delta = 0.063859700
2023-10-27_15_52_50_156: EngineState: * R = 5600.000000000, Rmeasured = 5264.385742176, Rest = 5487.410644544, Creal = 0.936384768
2023-10-27_15_52_50_157: EngineState: *** Resistor R2...
2023-10-27_15_52_50_157: EngineState: pin_markUsed: boardId on PD8
2023-10-27_15_52_50_158: EngineState: * dTime2-1 = 2464
2023-10-27_15_52_50_159: EngineState: * dTime3-2 = 2464
2023-10-27_15_52_50_159: EngineState: * dTime4-3 = 1499
2023-10-27_15_52_50_160: EngineState: * Tc1 = 616.000000000, Tc2 = 374.750000000, Td = 616.000000000
2023-10-27_15_52_50_160: EngineState:
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

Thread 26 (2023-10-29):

outputs vaidation

rusefillc, 2023-10-29:
валидация платой-стимулятором не успешна

```
0/27 inj1 GOOD channel 1
1/27 inj2 GOOD channel 2
2/27 inj3 GOOD channel 3
3/27 inj4 GOOD channel 4
4/27 coil 1 GOOD channel 5
5/27 coil 2 GOOD channel 6
6/27 coil 3 GOOD channel 7
7/27 coil 4 GOOD channel 8
ERROR! Cycle 9@0 FAILED! (set 1, received 0 0.002v)
ERROR! Cycle 9@2 FAILED! (set 1, received 0 0.003v)
!!!!!!! BAD channel 9 pin 235 !!!!!!!!!!!!!!!
9/27 pin 101 GOOD channel 10
ERROR! Cycle 11@0 FAILED! (set 1, received 0 0.002v)
ERROR! Cycle 11@2 FAILED! (set 1, received 0 0.002v)
!!!!!!! BAD channel 11 pin 102 !!!!!!!!!!!!!!!
11/27 main Relay GOOD channel 12
12/27 pin 131 GOOD channel 13
13/27 pin 140 GOOD channel 14
14/27 Fan Relay GOOD channel 15
15/27 Fuel Relay GOOD channel 16
ERROR! Cycle 17@0 FAILED! (set 1, received 0 0.002v)
ERROR! Cycle 17@2 FAILED! (set 1, received 0 0.003v)
!!!!!!! BAD channel 17 pin 151 !!!!!!!!!!!!!!!
ERROR! Cycle 18@0 FAILED! (set 1, received 0 0.003v)
ERROR! Cycle 18@2 FAILED! (set 1, received 0 0.002v)
!!!!!!! BAD channel 18 pin 152 !!!!!!!!!!!!!!!
ERROR! Cycle 19@0 FAILED! (set 1, received 0 0.003v)
ERROR! Cycle 19@2 FAILED! (set 1, received 0 0.002v)
!!!!!!! BAD channel 19 (null) !!!!!!!!!!!!!!!
```

для начала фокусируюсь на первом сломанном pin 235

отключил провод от платы-стимулятора, одел мултиметр на землю в ржиме писка

с одной стороны, слышу двойной писк в момент отсылки CAN команд на тестирование всех

с другой стороны, не слышу реакции на попытки прямого управления пином

```
bench_setpin pD15
bench_clearpin pD15
```

rusefillc, 2023-10-29:
@Qwerty-OFF или вот другой инструмент тестирования
244 & 101 пищат от тестовых кнопок, а 235 не пищит. пожет маппинг перепутан?

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

rusefillc, 2023-10-29:
так, на схеме наркомания и у меня 102 из маппинга управляет 235ым

1-2-3-4
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

немного странно
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

ещё странее - см. 2<>3
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

rusefillc, 2023-10-29:
```
bench_setpin pe2
bench_clearpin pe2

bench_setpin pb8
bench_clearpin pb8

```

rusefillc, 2023-10-29:
Some progress under https://github.com/rusefi/rusefi-hardware/issues/251

Closed 2023-10-29.

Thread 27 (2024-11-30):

aux_axis_origin is missing in the PCB file

kristsm, 2024-11-30:
Hi! I am getting this error when generating  new board rev, even if I use unmodified kicad hellen-112-17 project,  reset origins and place new Drill/Place origin at the bottom left corner of the PCB. I am using KiCad 8.0.6 on Linux.

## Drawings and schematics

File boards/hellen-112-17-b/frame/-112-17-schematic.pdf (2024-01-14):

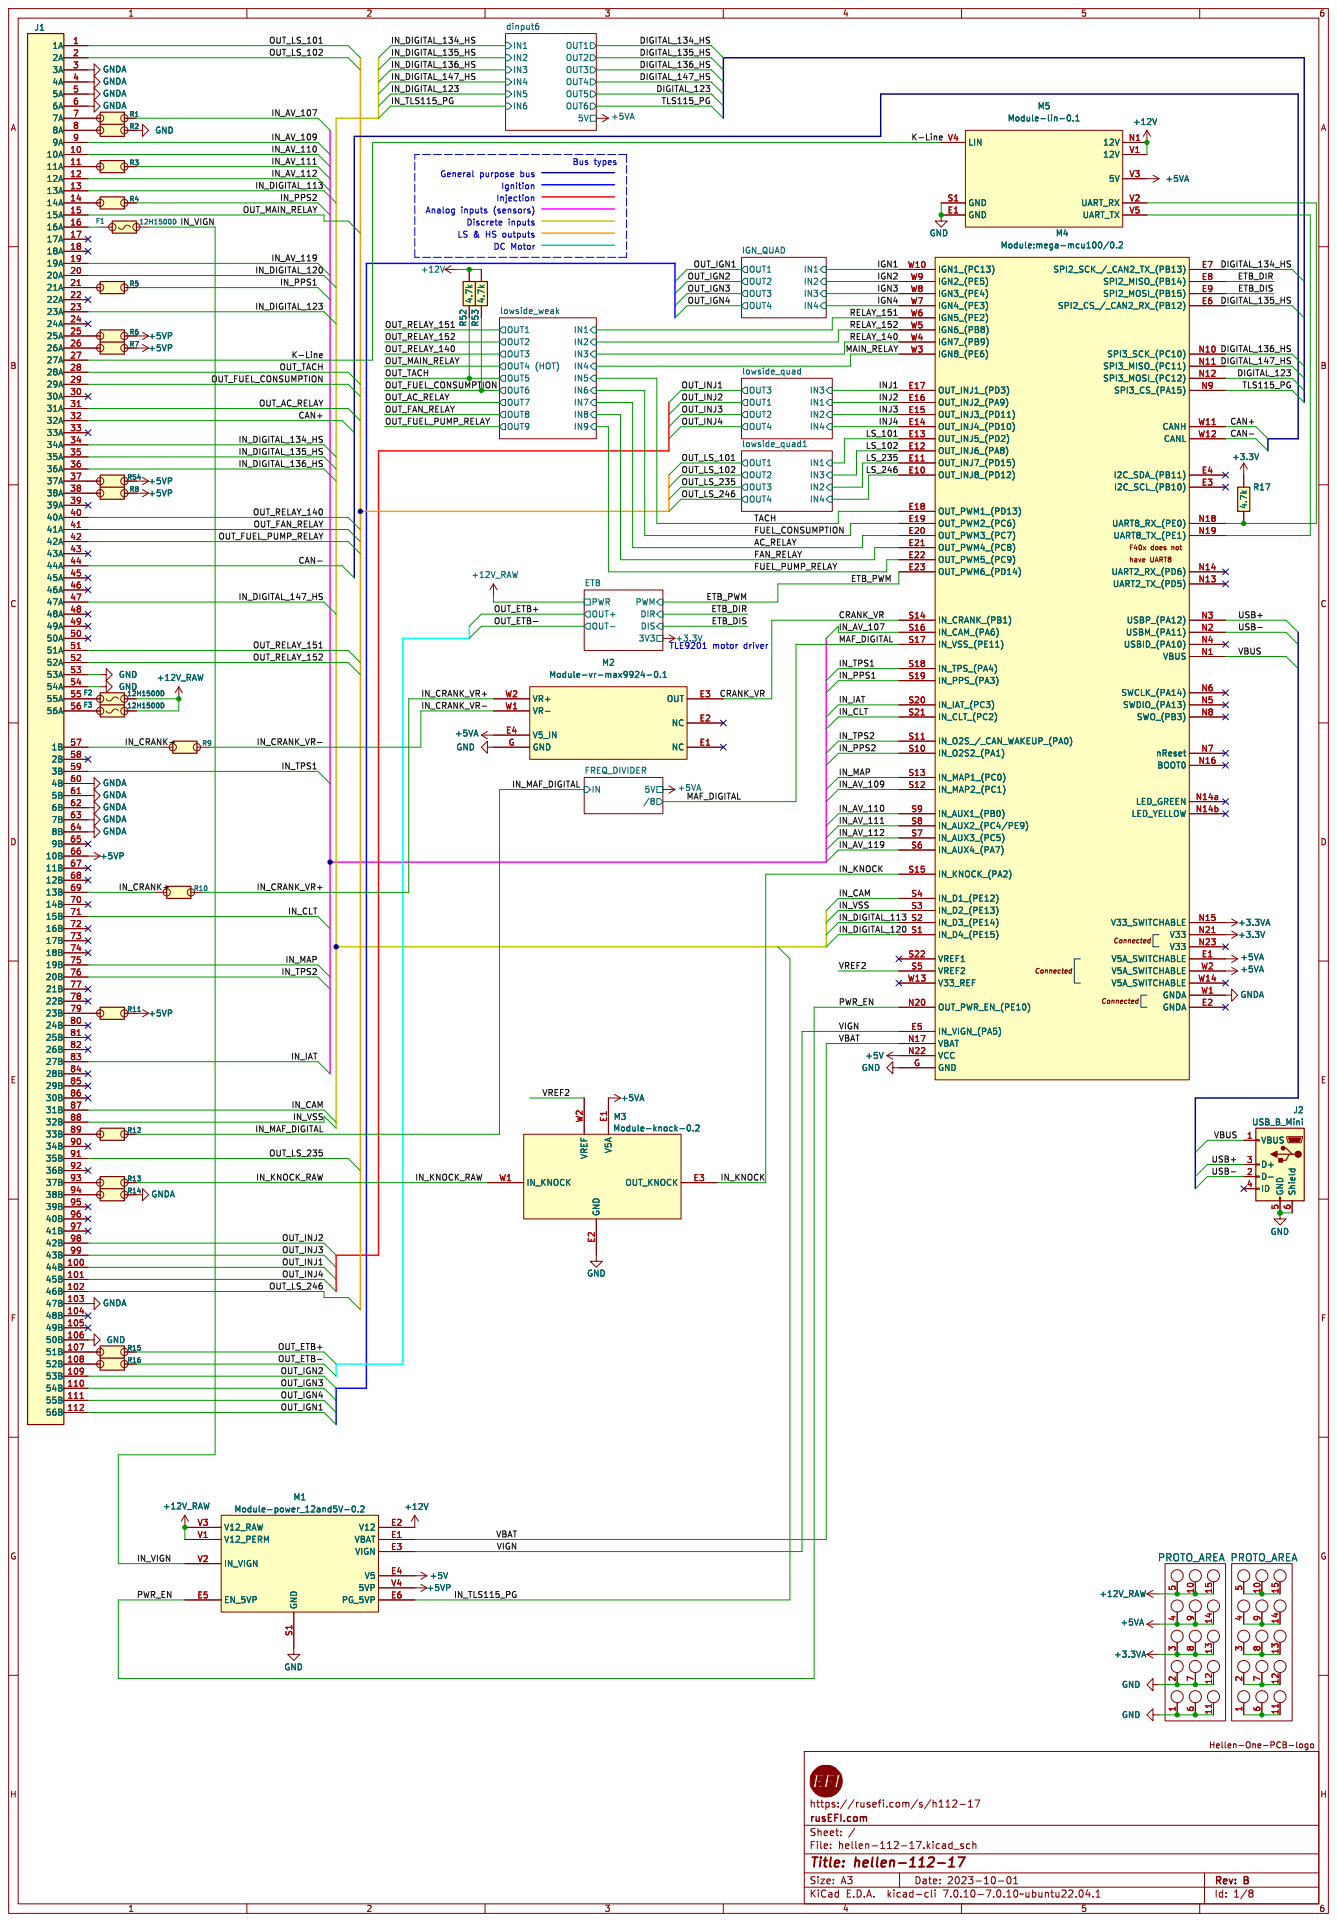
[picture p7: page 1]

Analog inputs (sensors) GNDA GNDA

Discrete inputs DC Motor
LS & HS outputs

Hellen-One-PCB-logo

https://rusefi.com/s/h112-17
File: hellen-112-17.kicad_sch Sheet: / rusEFI.com

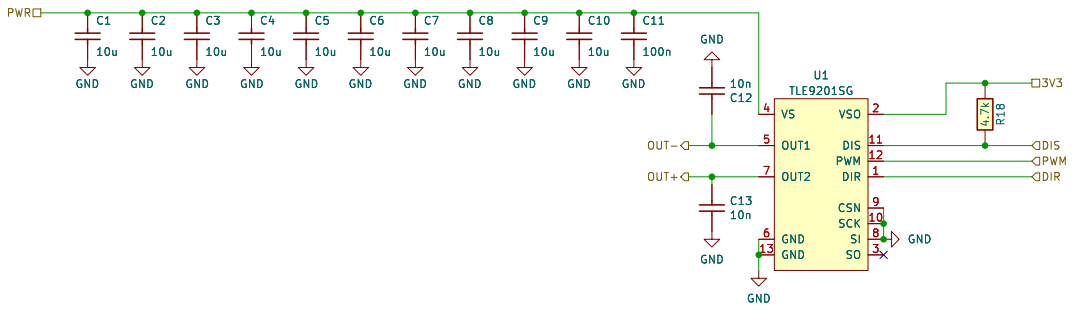
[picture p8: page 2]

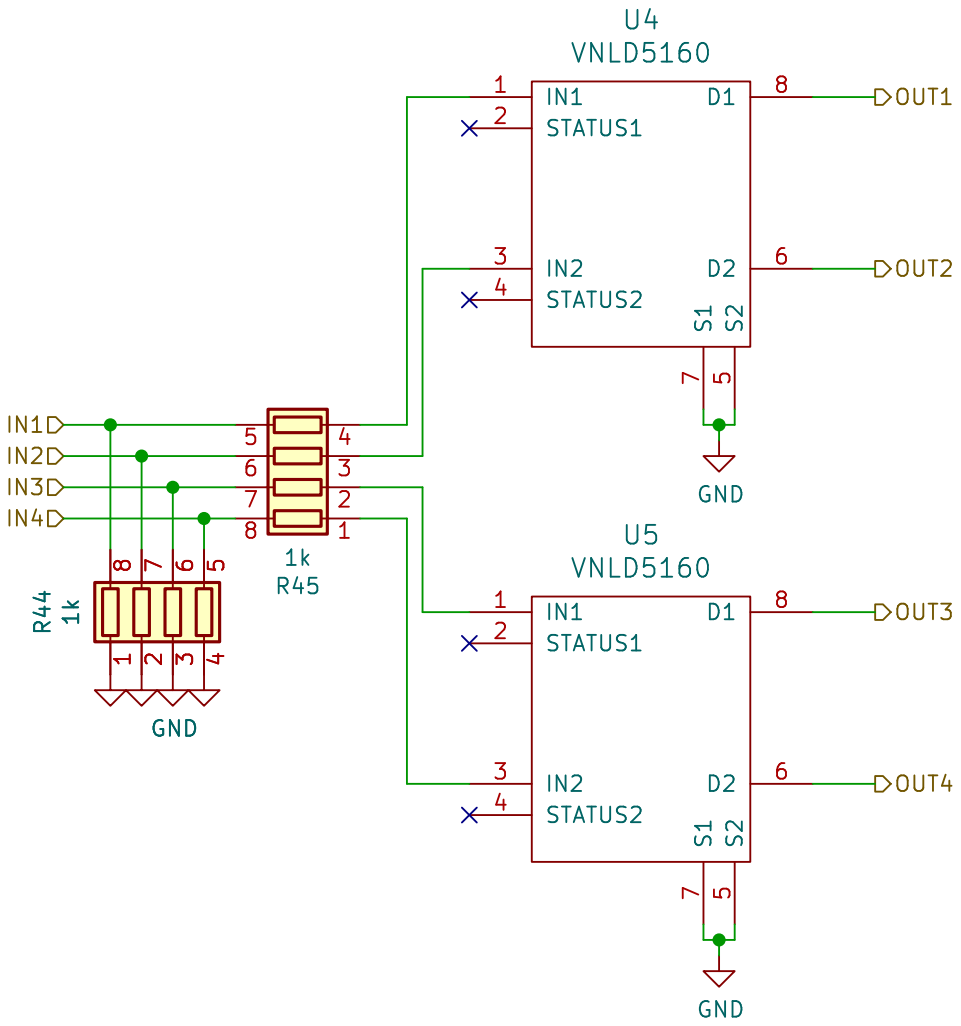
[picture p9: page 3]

Id: 3/8 Title: File: lowside_quad.kicad_sch Sheet: /lowside_quad/ rusEFI

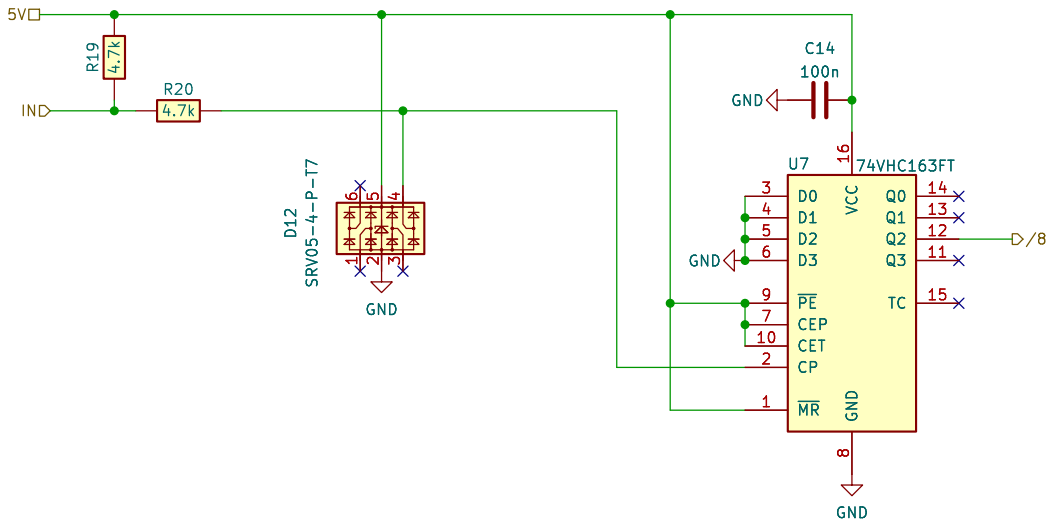
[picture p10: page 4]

Id: 4/8 Title: File: FREQ_DIVIDER.kicad_sch Sheet: /FREQ_DIVIDER/

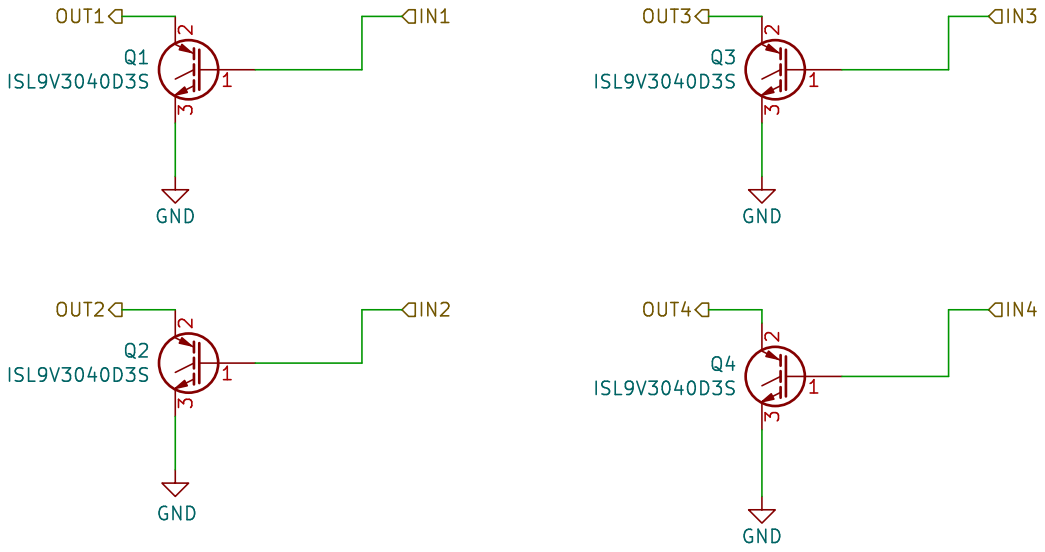
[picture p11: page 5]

Id: 5/8 Title: File: ign_quad.kicad_sch Sheet: /IGN_QUAD/ GND

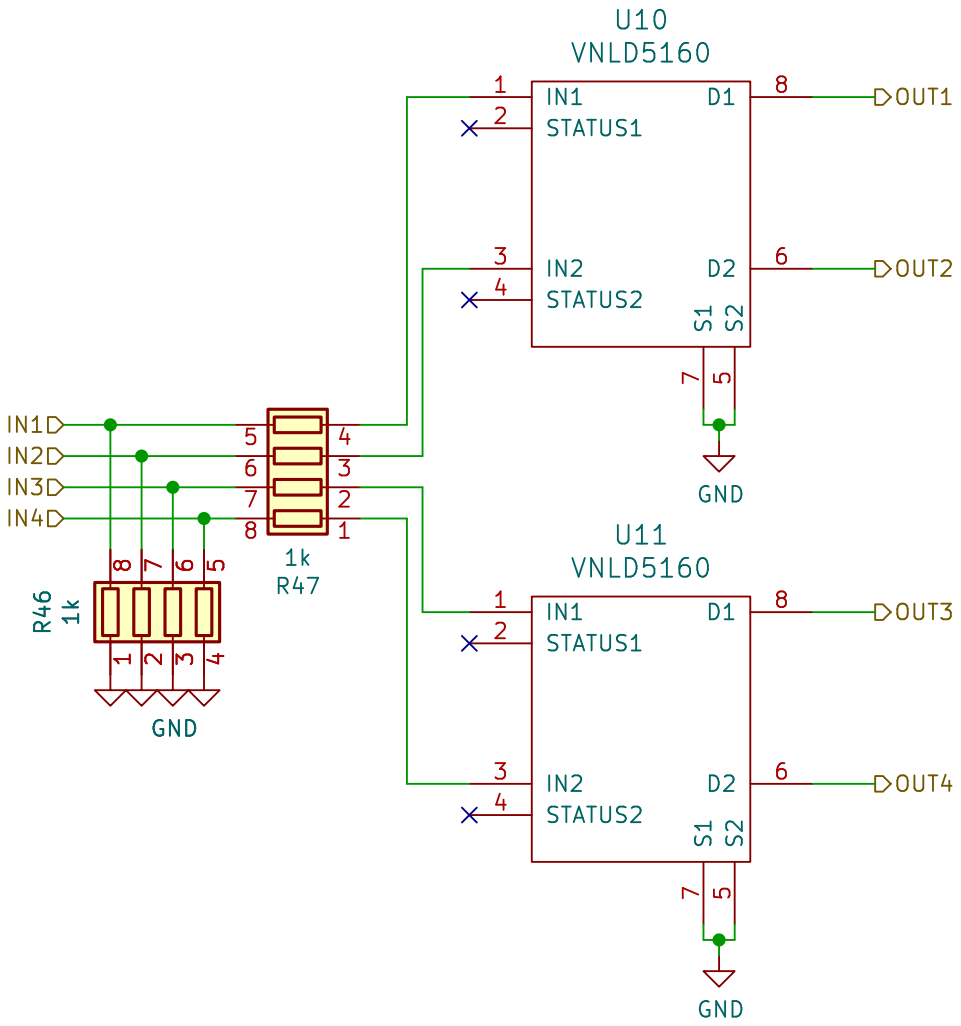
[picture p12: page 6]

Id: 6/8 Title: File: lowside_quad.kicad_sch Sheet: /lowside_quad1/ rusEFI

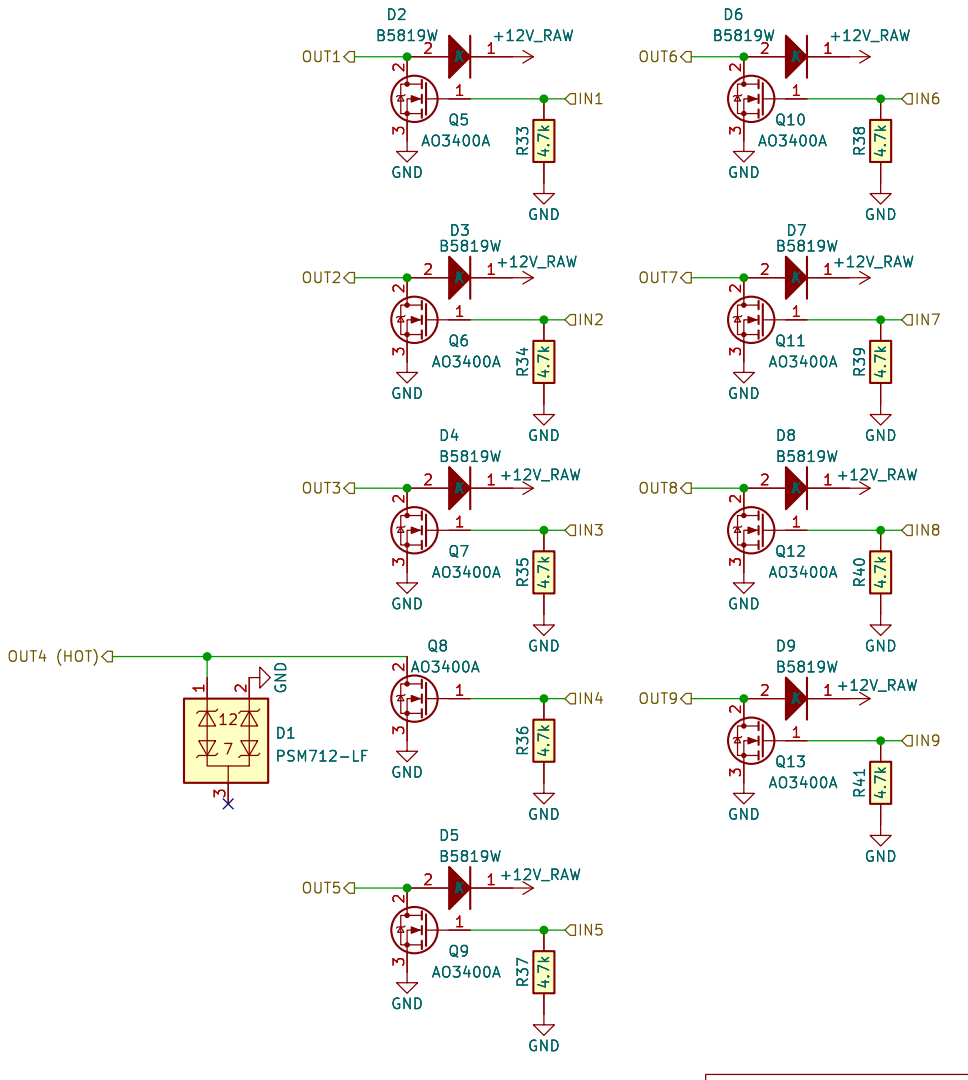
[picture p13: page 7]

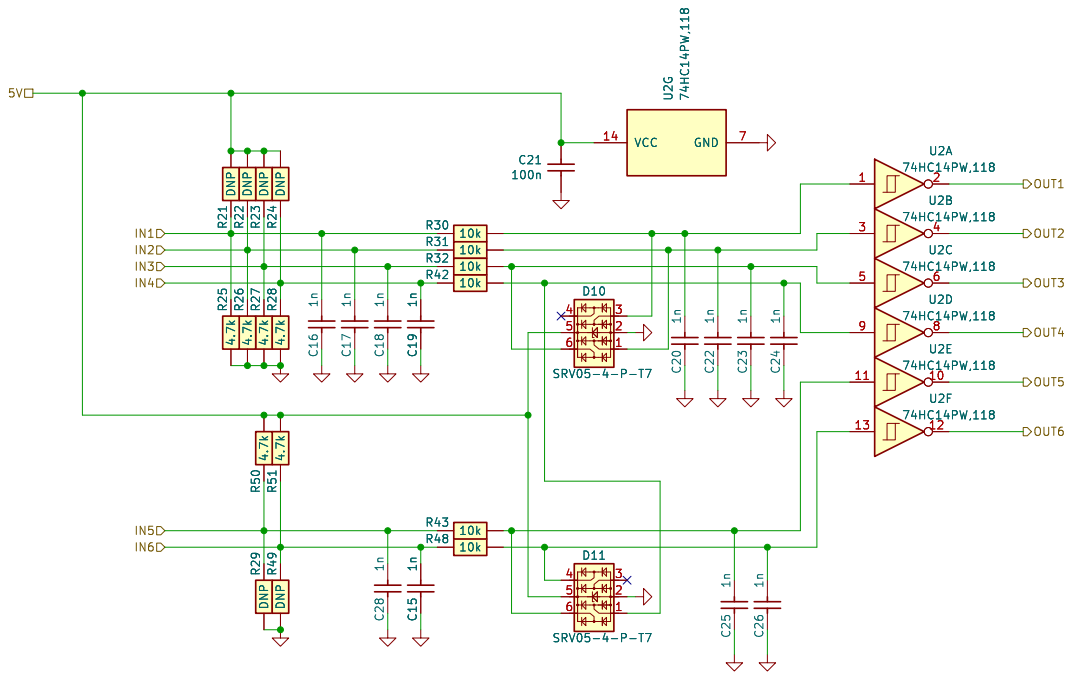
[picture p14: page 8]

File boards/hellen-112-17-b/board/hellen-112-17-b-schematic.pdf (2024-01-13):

# IGN_QUAD OUT3 OUT4 OUT2 OUT1 IN1

# R7 R8 R5 GND GND


Analog inputs (sensors) GNDA GNDA

Discrete inputs DC Motor
LS & HS outputs

Hellen-One-PCB-logo

https://rusefi.com/s/h112-17
File: hellen-112-17.kicad_sch Sheet: / rusEFI.com


D Date: 2023-10-01 KiCad; kicad-cli; 7.0.10-7.0.10~ubuntu22.04.1 Size: A4; Rev:; STATUS1 2; STATUS2 4; 7 D1 8 U4 VNLD5160; GND GND; GND; 5 R44 1kIN1 1 STATUS1 2; 7 D1 8 U5 VNLD5160 OUT1 OUT2; OUT3 OUT4; GND R⁴⁴ ¹k

Id: 3/8 Title: File: lowside_quad.kicad_sch Sheet: /lowside_quad/ rusEFI


Id: 4/8 Title: File: FREQ_DIVIDER.kicad_sch Sheet: /FREQ_DIVIDER/

D Date: KiCad; kicad-cli; 7.0.10-7.0.10~ubuntu22.04.1 Size: A4; Rev:; ISL9V3040D3S GND; ISL9V3040D3S; 2 3 Q3 ISL9V3040D3S GND; IN2 OUT1; OUT3 OUT2; OUT4

Id: 5/8 Title: File: ign_quad.kicad_sch Sheet: /IGN_QUAD/ GND

D Date: 2023-10-01 KiCad; kicad-cli; 7.0.10-7.0.10~ubuntu22.04.1 Size: A4; Rev:; STATUS1 2; STATUS2 4; 7 D1 8 U10 VNLD5160; GND GND; 5 R46 1k GND; 7 D1 8 U11 VNLD5160 OUT1 OUT2; OUT3 OUT4; GND R⁴⁶ ¹k

Id: 6/8 Title: File: lowside_quad.kicad_sch Sheet: /lowside_quad1/ rusEFI

+12V_RAW R⁴¹ 4.7k GND | GND R³⁹ 4.7k R³³ 4.7k | GND | R³⁸ 4.7k 1 ² 3 | Q10 AO3400A K | 1 A 2 D6 B5819W | +12V_RAW
IN3 | OUT6



74HC14PW,118 R²⁹ DNP R⁴⁹ DNP

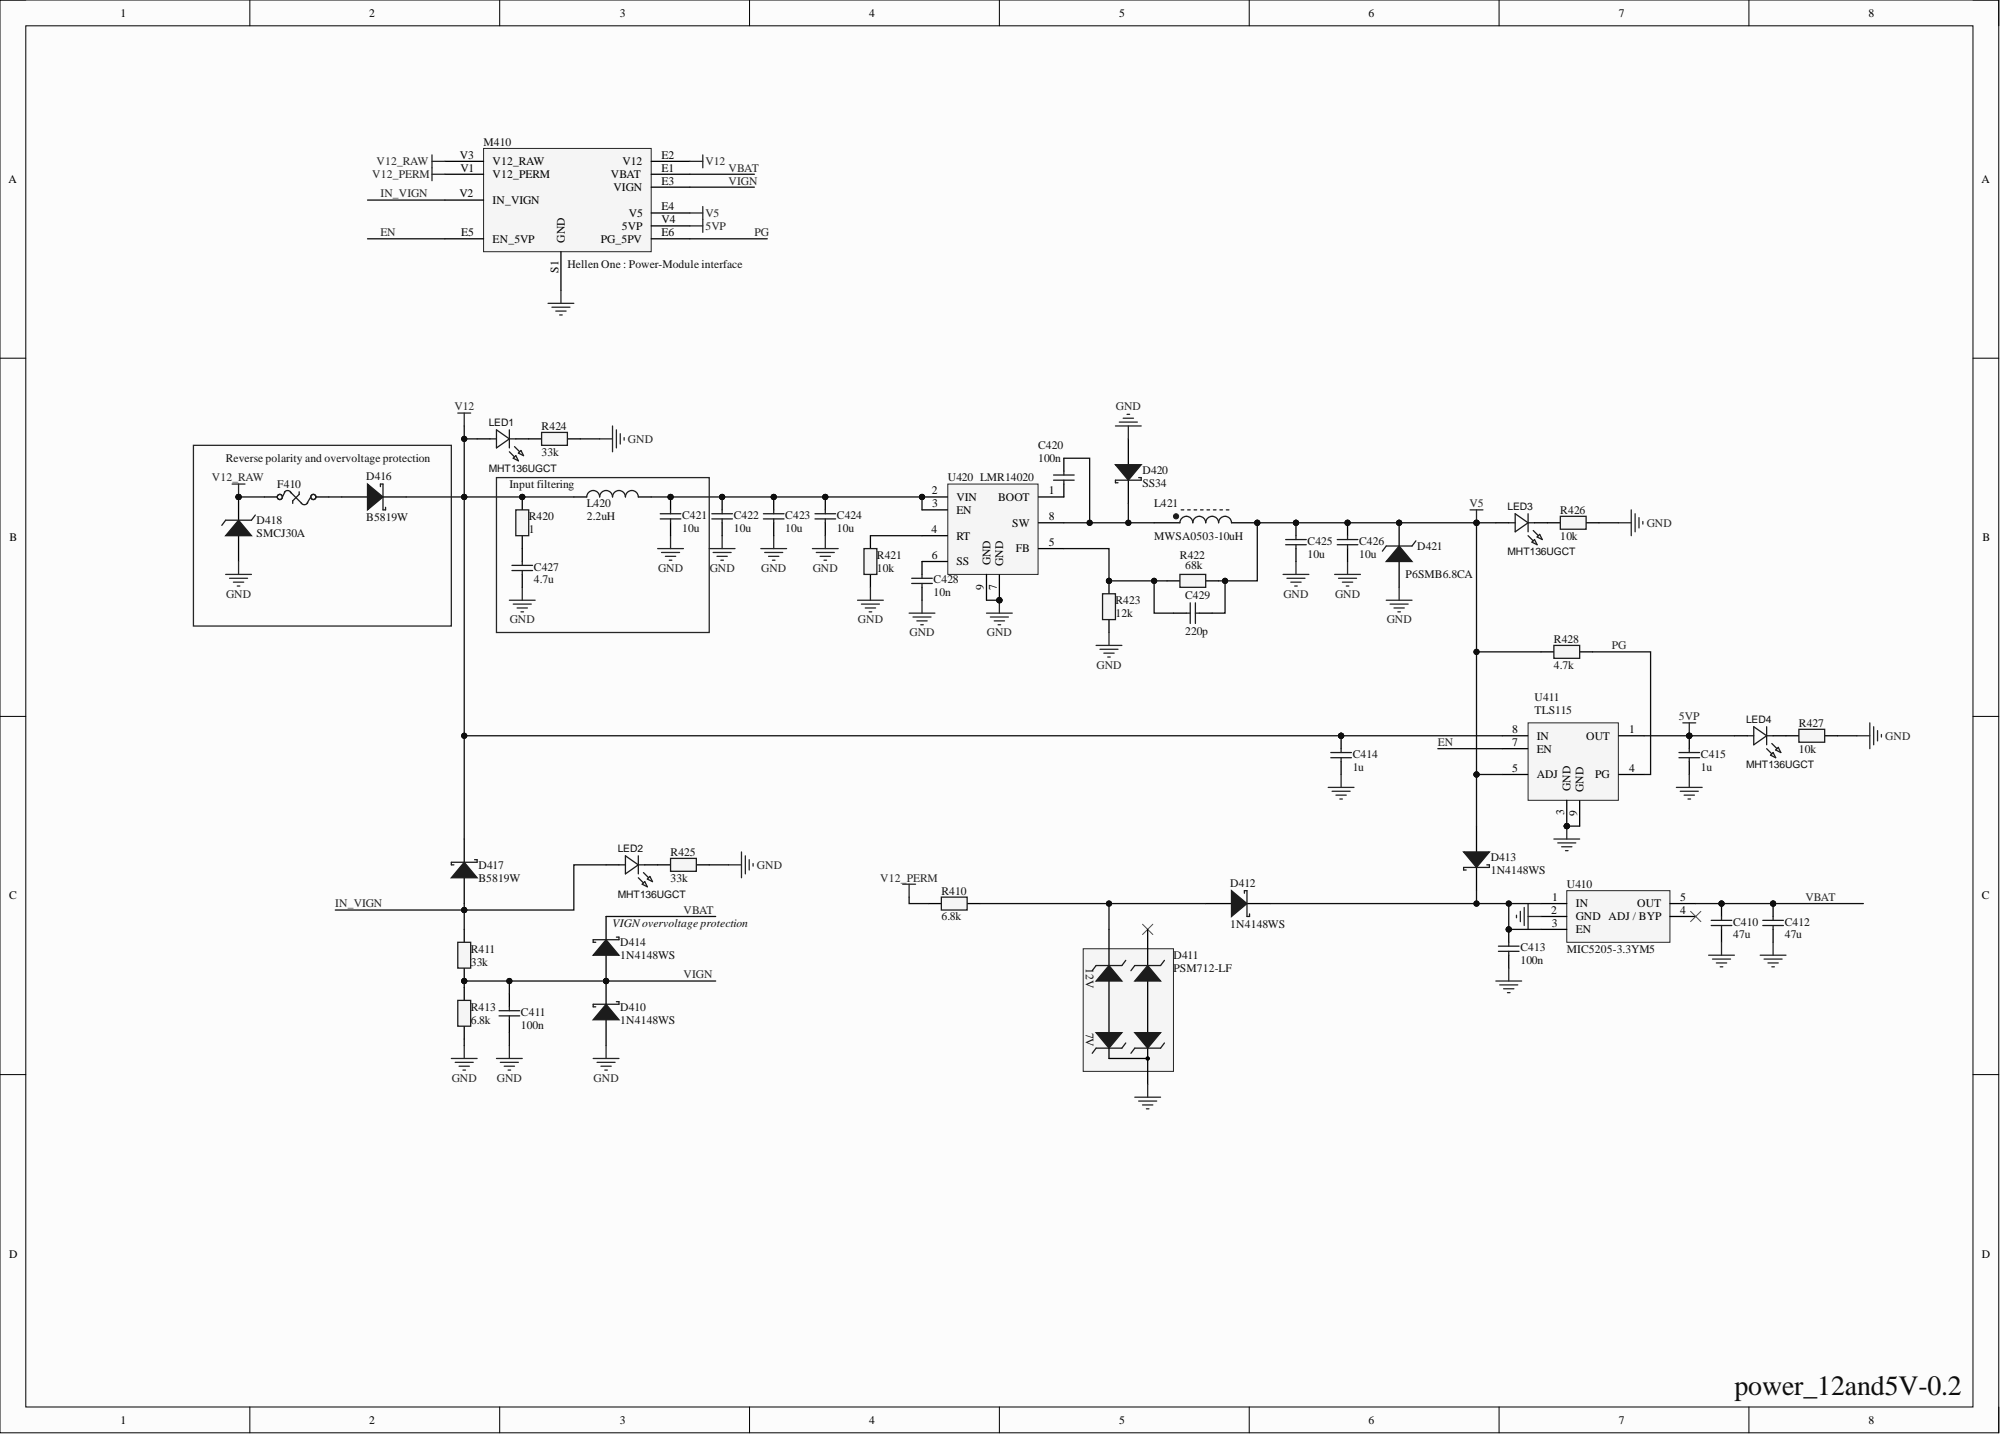
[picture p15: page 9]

Hellen One : Power-Module interface

Reverse polarity and overvoltage protection
F410 V12_RAW

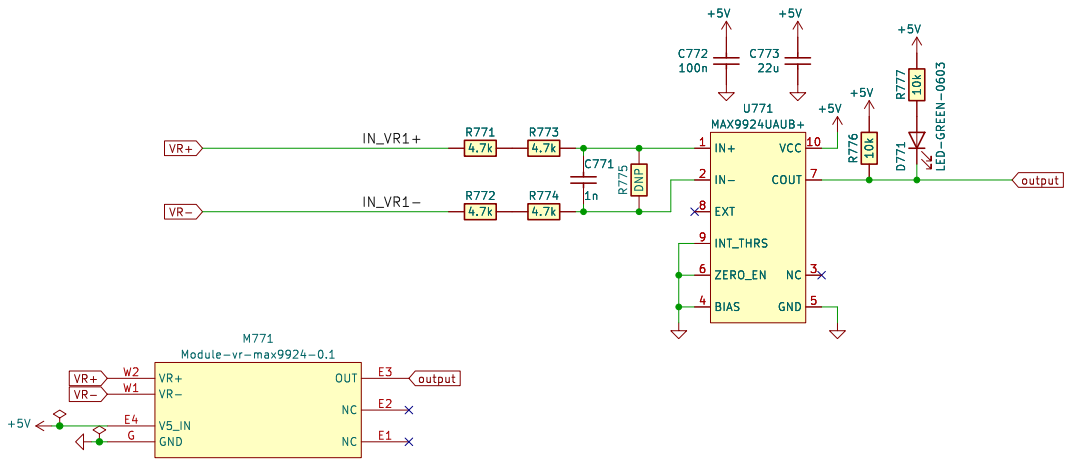
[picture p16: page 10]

Id: 1/1 Title: VR MAX9924 module

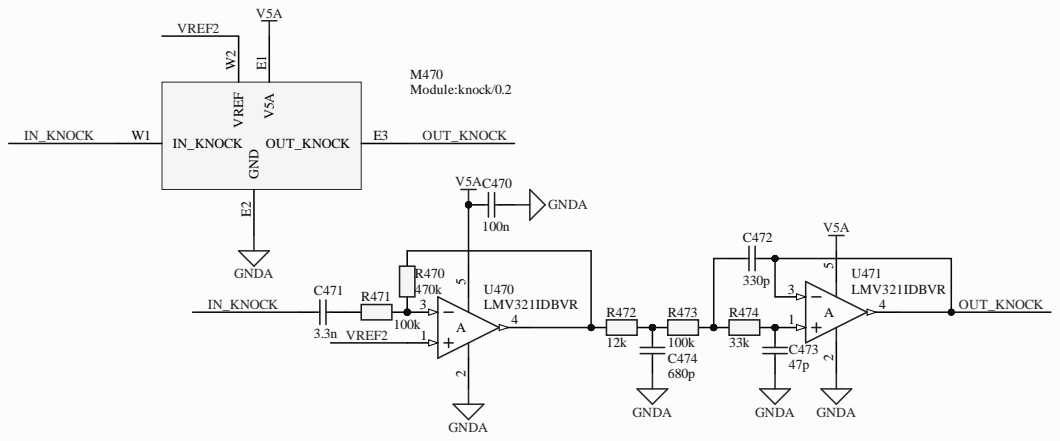
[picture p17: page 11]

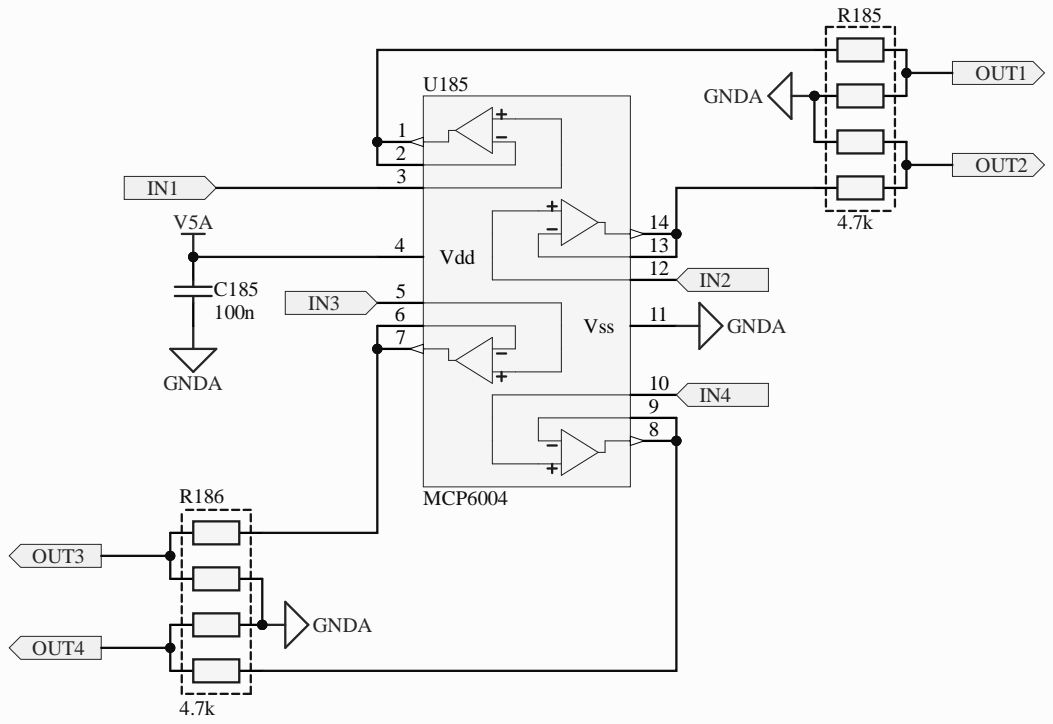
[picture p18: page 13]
Vdd 4; Vss 6; MCP6004; GNDA; OUT1; OUT2; OUT3; OUT4; C185 PIC18501 100n; PIC18502 COC3; PIR18501; PIR18502; PIR18503; PIR18504; PIR18505; PIR18506; PIR18507; PIR18508; COR5; PIR18601; PIR18602; PIR18603; PIR18605; PIR18604; PIR18606; PIR18607; PIR18608; COR6; PIU18501; PIU18502; PIU18503; PIU18504; PIU18505; PIU18506; PIU18507; PIU18508; PIU18509; PIU185010; PIU185011; PIU185012; PIU185013; PIU185014; COU2; PIC18501; POOUT2; POOUT1; POOUT3; POOUT4; POIN1; POIN3 PIU18505; PIU185010 POIN4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

Vdd 4; Vss 6; MCP6004; GNDA; OUT1; OUT2; OUT3; OUT4; C190 PIC19001 100n; PIC19002 COC3; PIR19001; PIR19002; PIR19003; PIR19004; PIR19005; PIR19006; PIR19007; PIR19008; COR5; PIR19101; PIR19102; PIR19103; PIR19105; PIR19104; PIR19106; PIR19107; PIR19108; COR6; PIU19001; PIU19002; PIU19003; PIU19004; PIU19005; PIU19006; PIU19007; PIU19008; PIU19009; PIU190010; PIU190011; PIU190012; PIU190013; PIU190014; COU2; PIC19001; POOUT2; POOUT1; POOUT3; POOUT4; POIN1; POIN3 PIU19005; PIU190010 POIN4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

SPI_; VCC; 5 SPI_SCK; 7 SPI_O; lex MicroSD; _MIS


R143 populated: analog input O2S
R145 populated: WAKEUP by CAN

*VIGN input is unprotected!
*A21 is duplicated for ADC and EINT




D100 PESD1CAN; GND; TXD 1 GND 2 VCC 3; Vio; 5 RXD 4; CANL; 6 CANH; TJA1051T/3/1J; CAN_TX; CAN_RX; VCC; CANH; CANL C100 100n

VRE; _CRA; _CLT; IAT; _IAT; VIG; nRes; VBAT; SWCL; SPI2; _MIS; SPI3; I2C_SCL; SPI1; PWR_; GRE; u mcu.Sch; _IGN; 8.Sch; n can.Sch; d.Sch; nRS; USB_; P USB_; USBI; A I2C_SCL UART8_RX UART8_TX UART2_RX UART2_TX; N VBAT; VCC; ACC_SC; ACC_; ACC_MIS; ACC_MO; BARO; sen; ors.Sc; LVC1; VBU; wer.Sch; USBID (PA; USBM (PA; USBP (PA; 8 SWDIO (PA13); N5 SWCLK (PA14); N6 nReset; _SCK (PC1; _MISO (PC1; _MOSI (PC1; I2C_SCL (PB1; 3 I2C_SDA (PB11); E4 UART2_TX (PD5); _SCK; _MISO (PB1; _MOSI (PB1; _PWM2 (PC6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

USBM USBP USBID VBUS
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

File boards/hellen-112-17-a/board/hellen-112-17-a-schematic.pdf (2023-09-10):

# R4 GNDA

OUT_INJ8_(PD12) E10 | OUT_INJ7_(PD15) E11 | OUT_INJ6_(PA8) E12 | OUT_INJ5_(PD2) E13 | OUT_INJ4_(PD10) E14 | OUT_INJ3_(PD11) E15 | OUT_INJ2_(PA9) E16 | OUT_INJ1_(PD3) E17 | OUT_PWM1_(PD13) E18 | OUT_PWM2_(PC6) E19 | GNDA | E2


Analog inputs (sensors) DC Motor LS & HS outputs

GNDA GNDA

Hellen-One-PCB-logo

https://rusefi.com/s/h112-17
File: hellen-112-17.kicad_sch Sheet: / rusEFI.com


D Date: 2022-04-09 KiCad; kicad-cli; 7.0.7-7.0.7~ubuntu22.04.1 Size: A4; Rev: v0.7; 5 R44 1k GND; STATUS1 2; STATUS2 4; 7 D1 8 U4 VNLD5160 GND GND; 7 D1 8 U5 VNLD5160 OUT2 OUT1; OUT3 OUT4 Locate output; caps near; connector; pin; GND R⁴⁴ ¹k

rusefi.com/s/proteus
File: lowside_quad.kicad_sch Sheet: /lowside_quad/ rusEFI github.com/mck1117/proteus

Id: 3/8 Title: rusEfi Proteus


Id: 4/8 Title: File: FREQ_DIVIDER.kicad_sch Sheet: /FREQ_DIVIDER/

D Date: KiCad; kicad-cli; 7.0.7-7.0.7~ubuntu22.04.1 Size: A4; Rev:; ISL9V3040D3S GND; ISL9V3040D3S; 2 3 Q3 ISL9V3040D3S GND; IN2 OUT1; OUT3 OUT2; OUT4

Id: 5/8 Title: File: ign_quad.kicad_sch Sheet: /IGN_QUAD/ GND

D Date: 2022-04-09 KiCad; kicad-cli; 7.0.7-7.0.7~ubuntu22.04.1 Size: A4; Rev: v0.7; rusefi.com/s/proteus GND; GND; STATUS1 2; STATUS2 4; 7 D1 8 U10 VNLD5160; 5 R46 1k GND; 7 D1 8 U11 VNLD5160 OUT2 OUT1; OUT3 OUT4 Locate output; caps near; connector; pin; GND R⁴⁶ ¹k

File: lowside_quad.kicad_sch Sheet: /lowside_quad1/ rusEFI github.com/mck1117/proteus

Id: 6/8 Title: rusEfi Proteus

+12V_RAW R⁴¹ 4.7k GND | GND R³⁹ 4.7k R³³ 4.7k | GND | R³⁸ 4.7k 1 ² 3 | Q10 AO3400A K | 1 A 2 D6 B5819W | +12V_RAW
IN3 | OUT6



74HC14PW,118 R²⁹ DNP R⁴⁹ DNP


Hellen One : Power-Module interface

Reverse polarity and overvoltage protection
F410 V12_RAW


Id: 1/1 Title: VR MAX9924 module


Vdd 4; Vss 6; MCP6004; GNDA; OUT1; OUT2; OUT3; OUT4; C180 PIC18001 100n; PIC18002 COC3; PIR18001; PIR18002; PIR18003; PIR18004; PIR18005; PIR18006; PIR18007; PIR18008; COR5; PIR18101; PIR18102; PIR18103; PIR18105; PIR18104; PIR18106; PIR18107; PIR18108; COR6; PIU18001; PIU18002; PIU18003; PIU18004; PIU18005; PIU18006; PIU18007; PIU18008; PIU18009; PIU180010; PIU180011; PIU180012; PIU180013; PIU180014; COU2; PIC18001; POOUT2; POOUT1; POOUT3; POOUT4; POIN1; POIN3 PIU18005; PIU180010 POIN4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

Vdd 4; Vss 6; MCP6004; GNDA; OUT1; OUT2; OUT3; OUT4; C190 PIC19001 100n; PIC19002 COC3; PIR19001; PIR19002; PIR19003; PIR19004; PIR19005; PIR19006; PIR19007; PIR19008; COR5; PIR19101; PIR19102; PIR19103; PIR19105; PIR19104; PIR19106; PIR19107; PIR19108; COR6; PIU19001; PIU19002; PIU19003; PIU19004; PIU19005; PIU19006; PIU19007; PIU19008; PIU19009; PIU190010; PIU190011; PIU190012; PIU190013; PIU190014; COU2; PIC19001; POOUT2; POOUT1; POOUT3; POOUT4; POIN1; POIN3 PIU19005; PIU190010 POIN4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

SPI_; VCC; 5 SPI_SCK; 7 SPI_O; lex MicroSD; _MIS


R143 populated: analog input O2S
R145 populated: WAKEUP by CAN

*VIGN input is unprotected!
*A21 is duplicated for ADC and EINT




D100 PESD1CAN; GND; TXD 1 GND 2 VCC 3; Vio; 5 RXD 4; CANL 6 CANH; TJA1051T/3/1J; CAN_TX; CAN_RX; VCC; CANH; CANL C100 100n

VRE; _CRA; _CLT; IAT; _IAT; VIG; nRes; VBAT; SWCL; SPI2; _MIS; SPI3; I2C_SCL; SPI1; PWR_; u mcu.Sch; _IGN; 8.Sch; n can.Sch; d.Sch; nRS; USB_; P USB_; USBI; A I2C_SCL UART8_RX UART8_TX UART2_RX UART2_TX; N VBAT; VCC; ACC_SC; ACC_; ACC_MIS; ACC_MO; BARO; sen; ors.Sc; LVC1; VBU; wer.Sch; USBID (PA; USBM (PA; USBP (PA; 8 SWDIO (PA13); N5 SWCLK (PA14); N6 nReset; _SCK (PC1; _MISO (PC1; _MOSI (PC1; I2C_SCL (PB1; 3 I2C_SDA (PB11); E4 UART2_TX (PD5); _SCK; _MISO (PB1; _MOSI (PB1; _PWM2 (PC6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

USBM USBP USBID VBUS
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

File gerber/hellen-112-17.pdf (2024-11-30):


Analog inputs (sensors) GNDA GNDA

Discrete inputs DC Motor
LS & HS outputs

Hellen-One-PCB-logo

https://rusefi.com/s/h112-17
File: hellen-112-17.kicad_sch Sheet: / rusEFI.com



Id: 3/8 Title: File: lowside_quad.kicad_sch Sheet: /lowside_quad/ rusEFI


Id: 4/8 Title: File: FREQ_DIVIDER.kicad_sch Sheet: /FREQ_DIVIDER/


Id: 5/8 Title: File: ign_quad.kicad_sch Sheet: /IGN_QUAD/ GND


Id: 6/8 Title: File: lowside_quad.kicad_sch Sheet: /lowside_quad1/ rusEFI



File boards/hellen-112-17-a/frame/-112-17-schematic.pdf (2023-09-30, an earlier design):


Analog inputs (sensors) DC Motor LS & HS outputs

GNDA GNDA

Hellen-One-PCB-logo

https://rusefi.com/s/h112-17
File: hellen-112-17.kicad_sch Sheet: / rusEFI.com



rusefi.com/s/proteus
File: lowside_quad.kicad_sch Sheet: /lowside_quad/ rusEFI github.com/mck1117/proteus

Id: 3/8 Title: rusEfi Proteus


Id: 4/8 Title: File: FREQ_DIVIDER.kicad_sch Sheet: /FREQ_DIVIDER/


Id: 5/8 Title: File: ign_quad.kicad_sch Sheet: /IGN_QUAD/ GND


File: lowside_quad.kicad_sch Sheet: /lowside_quad1/ rusEFI github.com/mck1117/proteus

Id: 6/8 Title: rusEfi Proteus



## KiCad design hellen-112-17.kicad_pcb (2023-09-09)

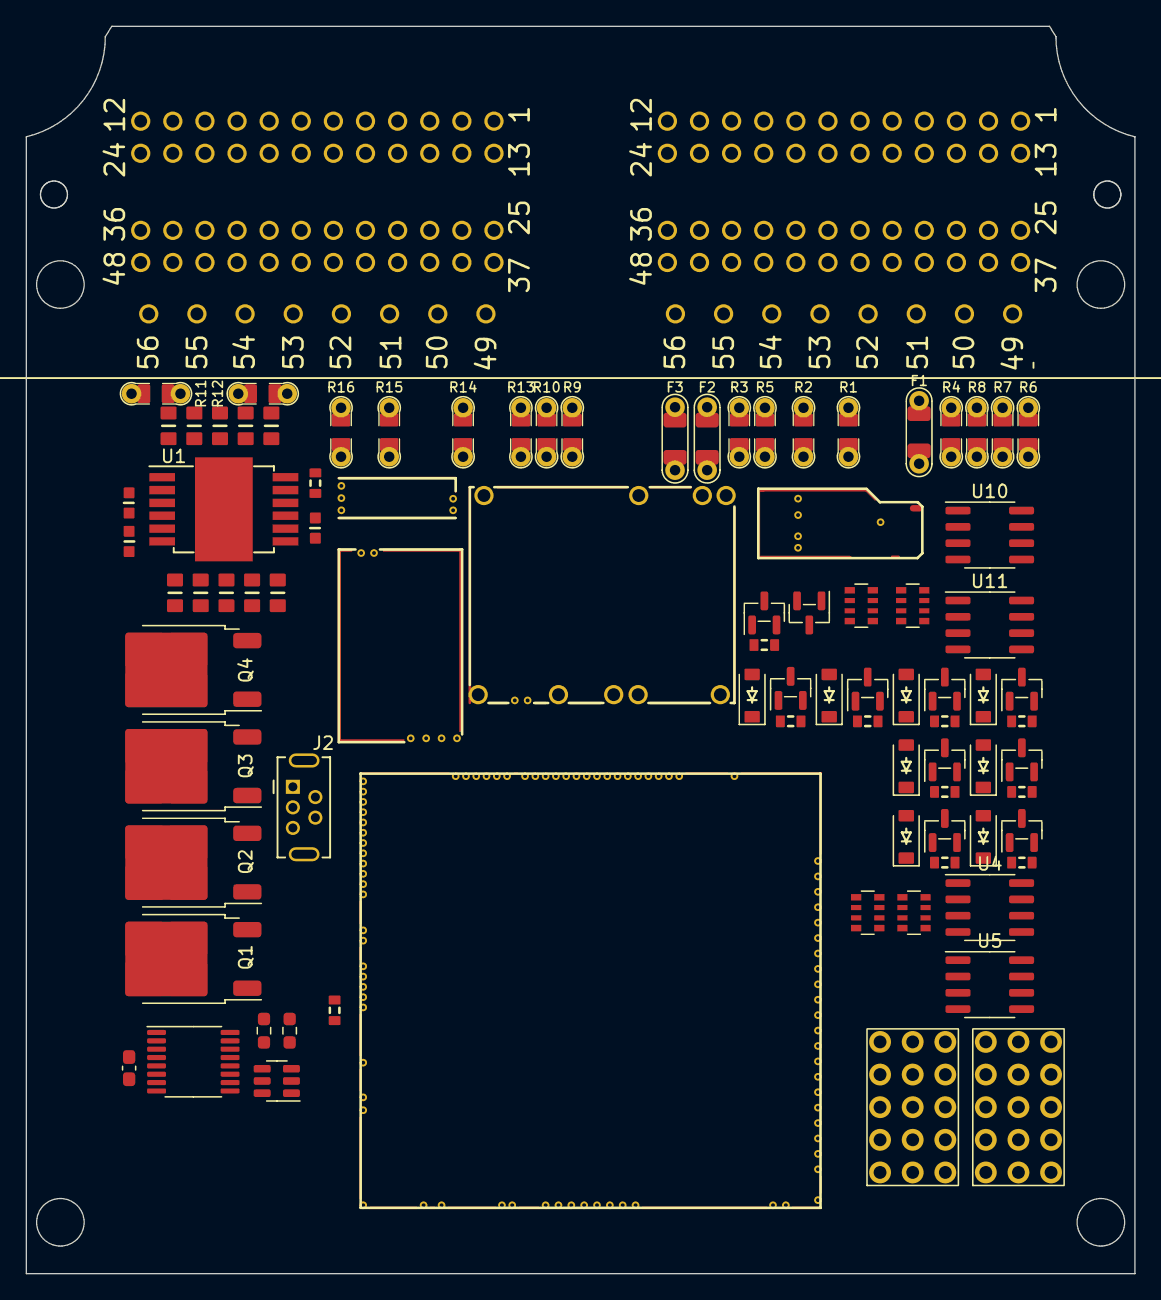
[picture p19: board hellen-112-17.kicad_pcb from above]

Board: 2 copper layers, 86.3 x 97.1 mm, 88 parts (0 on the bottom side), 132 nets, no tracks yet.

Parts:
C1, C2, C3, C4, C5, C6, C7, C8, C9, C10: 10u; C0805
C11: 100n; C0603
C12, C13: 10n; C0603
C14: 100n; C_0603_1608Metric_Pad1.08x0.95mm_HandSolder
D1: PSM712-LF; SOT-23
D2, D3, D4, D5, D6, D7, D8, D9: B5819W; SOD-123
F1, F2, F3: 12H1500D; PAD-1206-PAD
G1, G2: PROTO_AREA
J1: rusefi_2x56_pin_conn; rusefi_2x56_pin_connector
J2: USB_B_Mini; USB-MINI-B-VERTICAL
M1: Module-power_12and5V-0.2; power_12and5V
M2: Module-vr-max9924-0.1; vr-max9924
M3: Module-knock-0.2; knock
M4: Module:mega_mcu100/0.1; mega-mcu100
M5: Module-lin-0.1; lin
Q1, Q2, Q3, Q4: ISL9V3040D3S; TO-252-2
Q5, Q6, Q7, Q8, Q9, Q10, Q11, Q12, Q13: AO3400A; SOT-23
R1, R2, R3, R4, R5, R6, R7, R8, R9, R10, R11, R12, R13, R14, R15, R16: Jumper-Pad-Pad; PAD-0805-PAD
R17, R18, R33, R34, R35, R36, R37, R38, R39, R40, R41: 4.7k; R0603
R19, R20: 4.7k; R_0603_1608Metric_Pad0.98x0.95mm_HandSolder
R44, R45, R46, R47: 1k; R_Array_Convex_4x0603
U1: TLE9201SG; Infineon_PG-DSO-12-11
U4, U5, U10, U11: VNLD5160; SOIC-8_3.9x4.9mm_P1.27mm
U6: SRV05-4; SOT-23-6
U7: 74VHC163FT; TSSOP-16_4.4x5mm_P0.65mm

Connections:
+3.3V: M4.N21 (V33), R18.2, U1.2 (VSO)
+3.3VA: G1.3, G1.8, G1.13, M4.N15 (V33_SWITCHABLE)
+5V: M1.E4 (V5), M4.N22 (VCC)
+5VA: C14.2, G1.4, G1.9, G1.14, M2.E4 (V5_IN), M3.E1 (V5A), M4.E1 (V5A_SWITCHABLE), M4.W2 (V5A_SWITCHABLE), M5.V3 (5V), R19.2, U6.5 (VP), U7.1 (~MR), U7.7 (CEP), U7.9 (~PE), U7.10 (CET), U7.16 (VCC)
+5VP: J1.37, J1.66, M1.V4 (5VP), R6.2, R7.2, R8.2, R11.2
+12V: M1.E2 (V12), M5.N1 (12V), M5.V1 (12V)
+12V_RAW: C1.2, C2.2, C3.2, C4.2, C5.2, C6.2, C7.2, C8.2, C9.2, C10.2, C11.2, D2.1 (K), D3.1 (K), D4.1 (K), D5.1 (K), D6.1 (K), D7.1 (K), D8.1 (K), D9.1 (K), F2.2, F3.2, G1.5, G1.10, G1.15, M1.V1 (V12_PERM), M1.V3 (V12_RAW), U1.4 (VS)
/CAN+: J1.32, M4.W11 (CANH)
/CAN-: J1.44, M4.W12 (CANL)
/CRANK_VR: M2.E3 (OUT), M4.S14 (IN_CRANK_(PB1))
/ETB_DIR: M4.E8 (SPI2_MISO_(PB14)), U1.1 (DIR)
/ETB_DIS: M4.E9 (SPI2_MOSI_(PB15)), R18.1, U1.11 (DIS)
/ETB_PWM: M4.E23 (OUT_PWM6_(PD14)), U1.12 (PWM)
/IGN1: M4.W10 (IGN1_(PC13)), Q1.1 (G)
/IGN2: M4.W9 (IGN2_(PE5)), Q2.1 (G)
/IGN3: M4.W8 (IGN3_(PE4)), Q3.1 (G)
/IGN4: M4.W7 (IGN4_(PE3)), Q4.1 (G)
/INJ1: M4.E17 (OUT_INJ1_(PD3)), R44.8 (R1.2), R45.5 (R4.2)
/INJ2: M4.E16 (OUT_INJ2_(PA9)), R44.6 (R3.2), R45.7 (R2.2)
/INJ3: M4.E15 (OUT_INJ3_(PD11)), R44.7 (R2.2), R45.6 (R3.2)
/INJ4: M4.E14 (OUT_INJ4_(PD10)), R44.5 (R4.2), R45.8 (R1.2)
/IN_AV_107: M4.S16 (IN_CAM_(PA6)), R1.2
/IN_AV_109: J1.9, M4.S12 (IN_MAP2_(PC1))
/IN_AV_110: J1.10, M4.S9 (IN_AUX1_(PB0))
/IN_AV_111: M4.S8 (IN_AUX2_(PC4/PE9)), R3.2
/IN_AV_112: J1.12, M4.S7 (IN_AUX3_(PC5))
/IN_AV_119: J1.19, M4.S6 (IN_AUX4_(PA7))
/IN_CAM: J1.87, M4.S4 (IN_D1_(PE12))
/IN_CLT: J1.71, M4.S21 (IN_CLT_(PC2))
/IN_CRANK_VR+: M2.W2 (VR+), R10.2
/IN_CRANK_VR-: M2.W1 (VR-), R9.2
/IN_DIGITAL_113: J1.13, M4.S2 (IN_D3_(PE14))
/IN_DIGITAL_120: J1.20, M4.S1 (IN_D4_(PE15))
/IN_DIGITAL_123: J1.23, M4.E7 (SPI2_SCK_/_CAN2_TX_(PB13))
/IN_DIGITAL_134_HS: J1.34, M4.N10 (SPI3_SCK_(PC10))
/IN_DIGITAL_135_HS: J1.35, M4.N11 (SPI3_MISO_(PC11))
/IN_DIGITAL_136_HS: J1.36, M4.N9 (SPI3_CS_(PA15))
/IN_DIGITAL_147_HS: J1.47, M4.E6 (SPI2_CS_/_CAN2_RX_(PB12))
/IN_IAT: J1.83, M4.S20 (IN_IAT_(PC3))
/IN_KNOCK: M3.E3 (OUT_KNOCK), M4.S15 (IN_KNOCK_(PA2))
/IN_KNOCK_RAW: M3.W1 (IN_KNOCK), R13.2
/IN_MAF_DIGITAL: R12.2, R19.1, R20.2
/IN_MAP: J1.75, M4.S13 (IN_MAP1_(PC0))
/IN_PPS1: M4.S19 (IN_PPS_(PA3)), R5.2
/IN_PPS2: M4.S10 (IN_O2S2_(PA1)), R4.2
/IN_TPS1: J1.59, M4.S18 (IN_TPS_(PA4))
/IN_TPS2: J1.76, M4.S11 (IN_O2S_/_CAN_WAKEUP_(PA0))
/IN_VIGN: F1.2, M1.V2 (IN_VIGN)
/IN_VSS: J1.88, M4.S3 (IN_D2_(PE13))
/K-Line: J1.27, M5.V4 (LIN)
/MAF_DIGITAL: M4.S17 (IN_VSS_(PE11)), U7.12 (Q2)
/OUT_AC: D7.2 (A), J1.31, Q11.2 (D)
/OUT_ETB+: C13.2, R15.2, U1.7 (OUT2)
/OUT_ETB-: C12.2, R16.2, U1.5 (OUT1)
/OUT_FAN_RELAY: D8.2 (A), J1.41, Q12.2 (D)
/OUT_FUEL: D6.2 (A), J1.29, Q10.2 (D)
/OUT_FUEL_PUMP_RELAY: D9.2 (A), J1.42, Q13.2 (D)
/OUT_IGN1: J1.112, Q1.2 (C)
/OUT_IGN2: J1.109, Q2.2 (C)
/OUT_IGN3: J1.110, Q3.2 (C)
/OUT_IGN4: J1.111, Q4.2 (C)
/OUT_INJ1: J1.100, U4.8 (D1)
/OUT_INJ2: J1.98, U4.6 (D2)
/OUT_INJ3: J1.99, U5.8 (D1)
/OUT_INJ4: J1.101, U5.6 (D2)
/OUT_LS_101: J1.1, U10.8 (D1)
/OUT_LS_102: J1.2, U10.6 (D2)
/OUT_LS_235: J1.91, U11.8 (D1)
/OUT_LS_246: J1.102, U11.6 (D2)
/OUT_MAIN_RELAY: D1.1, J1.15, Q8.2 (D)
/OUT_RELAY_140: D4.2 (A), J1.40, Q7.2 (D)
/OUT_RELAY_151: D2.2 (A), J1.51, Q5.2 (D)
/OUT_RELAY_152: D3.2 (A), J1.52, Q6.2 (D)
/OUT_TACH: D5.2 (A), J1.28, Q9.2 (D)
/PWR_EN: M1.E5 (EN_5VP), M4.N20 (OUT_PWR_EN_(PE10))
/TLS115_PG: M1.E6 (PG_5VP), M4.N12 (SPI3_MOSI_(PC12))
/USB+: J2.3 (D+), M4.N3 (USBP_(PA12))
/USB-: J2.2 (D-), M4.N2 (USBM_(PA11))
/VBAT: M1.E1 (VBAT), M4.N17 (VBAT)
/VBUS: J2.1 (VBUS), M4.N1 (VBUS)
/VIGN: M1.E3 (VIGN), M4.E5 (IN_VIGN_(PA5))
/VREF2: M3.W2 (VREF), M4.S5 (VREF2)
/lowside_quad1/IN1: M4.E13 (OUT_INJ5_(PD2)), R46.8 (R1.2), R47.5 (R4.2)
/lowside_quad1/IN2: M4.E11 (OUT_INJ7_(PD15)), R46.7 (R2.2), R47.6 (R3.2)
/lowside_quad1/IN3: M4.E12 (OUT_INJ6_(PA8)), R46.6 (R3.2), R47.7 (R2.2)
/lowside_quad1/IN4: M4.E10 (OUT_INJ8_(PD12)), R46.5 (R4.2), R47.8 (R1.2)
/lowside_weak/IN1: M4.W6 (IGN5_(PE2)), Q5.1 (G), R33.1
/lowside_weak/IN2: M4.W5 (IGN6_(PB8)), Q6.1 (G), R34.1
/lowside_weak/IN3: M4.W4 (IGN7_(PB9)), Q7.1 (G), R35.1
/lowside_weak/IN4: M4.W3 (IGN8_(PE6)), Q8.1 (G), R36.1
/lowside_weak/IN5: M4.E18 (OUT_PWM1_(PD13)), Q9.1 (G), R37.1
/lowside_weak/IN6: M4.E19 (OUT_PWM2_(PC6)), Q10.1 (G), R38.1
/lowside_weak/IN7: M4.E20 (OUT_PWM3_(PC7)), Q11.1 (G), R39.1
/lowside_weak/IN8: M4.E21 (OUT_PWM4_(PC8)), Q12.1 (G), R40.1
/lowside_weak/IN9: M4.E22 (OUT_PWM5_(PC9)), Q13.1 (G), R41.1
GND: C1.1, C2.1, C3.1, C4.1, C5.1, C6.1, C7.1, C8.1, C9.1, C10.1, C11.1, C12.1, C13.1, C14.1, D1.2, G1.1, G1.2, G1.6, G1.7, G1.11, G1.12, J1.53, J1.54, J1.106, J2.5 (GND), J2.6 (Shield), M1.S1 (GND), M2.G (GND), M3.E2 (GND), M4.G (GND), M5.E1 (GND), M5.S1 (GND), Q1.3 (E), Q2.3 (E), Q3.3 (E), Q4.3 (E), Q5.3 (S), Q6.3 (S), Q7.3 (S), Q8.3 (S), Q9.3 (S), Q10.3 (S), Q11.3 (S), Q12.3 (S), Q13.3 (S), R2.2, R33.2, R34.2, R35.2, R36.2, R37.2, R38.2, R39.2, R40.2, R41.2, R44.1 (R1.1), R44.2 (R2.1), R44.3 (R3.1), R44.4 (R4.1), R46.1 (R1.1), R46.2 (R2.1), R46.3 (R3.1), R46.4 (R4.1), U1.6 (GND), U1.8 (SI), U1.9 (CSN), U1.10 (SCK), U1.13 (GND), U4.5 (S2), U4.7 (S1), U5.5 (S2), U5.7 (S1), U6.2 (VN), U7.3 (D0), U7.4 (D1), U7.5 (D2), U7.6 (D3), U7.8 (GND), U10.5 (S2), U10.7 (S1), U11.5 (S2), U11.7 (S1)
GNDA: J1.3, J1.4, J1.5, J1.6, J1.60, J1.61, J1.62, J1.63, J1.64, J1.103, M4.W1 (GNDA), R14.2
unnamed: F1.1, J1.16
unnamed: F2.1, J1.55
unnamed: F3.1, J1.56
unnamed: G2.1, G2.6, G2.11
unnamed: G2.5, G2.10, G2.15
unnamed: G2.2, G2.7, G2.12
unnamed: G2.3, G2.8, G2.13
unnamed: G2.4, G2.9, G2.14
unnamed: J1.7, R1.1
unnamed: J1.8, R2.1
unnamed: J1.11, R3.1
unnamed: J1.14, R4.1
unnamed: J1.21, R5.1
unnamed: J1.25, R6.1
unnamed: J1.26, R7.1
unnamed: J1.38, R8.1
unnamed: J1.57, R9.1
unnamed: J1.69, R10.1
unnamed: J1.79, R11.1
unnamed: J1.89, R12.1
unnamed: J1.93, R13.1
unnamed: J1.94, R14.1
unnamed: J1.107, R15.1
unnamed: J1.108, R16.1
unnamed: M4.N18 (UART8_RX_(PE0)), M5.V2 (UART_RX), R17.2
unnamed: M4.N19 (UART8_TX_(PE1)), M5.V5 (UART_TX)
unnamed: R45.1 (R1.1), U5.3 (IN2)
unnamed: R45.2 (R2.1), U5.1 (IN1)
unnamed: R45.3 (R3.1), U4.3 (IN2)
unnamed: R45.4 (R4.1), U4.1 (IN1)
unnamed: R47.1 (R1.1), U11.3 (IN2)
unnamed: R47.2 (R2.1), U11.1 (IN1)
unnamed: R47.3 (R3.1), U10.3 (IN2)
unnamed: R47.4 (R4.1), U10.1 (IN1)
unnamed: R20.1, U6.1 (IO1), U6.3 (IO2), U6.4 (IO3), U6.6 (IO4), U7.2 (CP)

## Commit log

2022-11-19 Init project
    [hellen-112-17.kicad_pcb, hellen-112-17.kicad_sch]
2023-09-05 #3 #4 #5 #6
    [DC_MOTOR_0.1.kicad_sch, hellen-112-17.kicad_pcb, hellen-112-17.kicad_sch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]
2023-09-05 пронумеровала, перенесла изменения на плату
    [DC_MOTOR_0.1.kicad_sch, hellen-112-17.kicad_pcb, hellen-112-17.kicad_sch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]
2023-09-09 Upd SCH
    [DC_MOTOR_0.1.kicad_sch, FREQ_DIVIDER.kicad_sch, LS_weak.kicad_sch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]
2023-09-10 [skip actions] Auto-generated board
    [hellen-112-17-B_Cu.gbl, hellen-112-17-B_Mask.gbs, hellen-112-17-B_Paste.gbp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]
2023-09-10 Update mm100, connector, replace
    [bom_replace_hellen-112-17-a.csv, hellen-112-17.kicad_sch]
2023-09-10 srv05 value fix
    [FREQ_DIVIDER.kicad_sch, dinput6.kicad_sch]
2023-09-10 Warnings fix
    [FREQ_DIVIDER.kicad_sch, dinput6.kicad_sch]
2023-09-10 #18, #19
    [hellen-112-17.kicad_sch]
2023-09-10 # STM32F407VGT6 is very cheap U105,"STM32F429VGT6","LQFP100","C12345"
    [bom_replace_hellen-112-17-a.csv]
2023-09-30 112-17-b copy of a
    [bom_replace_hellen-112-17-b.csv]
2024-11-30 [skip actions] Auto-generated board v2.1
    [hellen-112-17-B_Cu.gbl, hellen-112-17-B_Mask.gbs, hellen-112-17-B_Paste.gbp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]
